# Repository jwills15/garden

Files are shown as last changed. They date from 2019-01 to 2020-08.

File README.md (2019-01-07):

# Smart Garden
Python code and engineering documentation for the Smart Garden system designed for Biola's Organic Garden.

All Python code can be located in the "Python Code/GardenPi" folder. The main script is tiltled "main.py".

Created by Joshua Williams, Engineering Research Intern, Biola CPE Department, Summer 2018.

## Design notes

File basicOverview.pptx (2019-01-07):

## Organic Garden Automation

Joshua Williams

## Current Solution

- Filling all gravel beds 15 minutes on, 45 minutes off
- Manual tank filling
- No oxygen level measurements

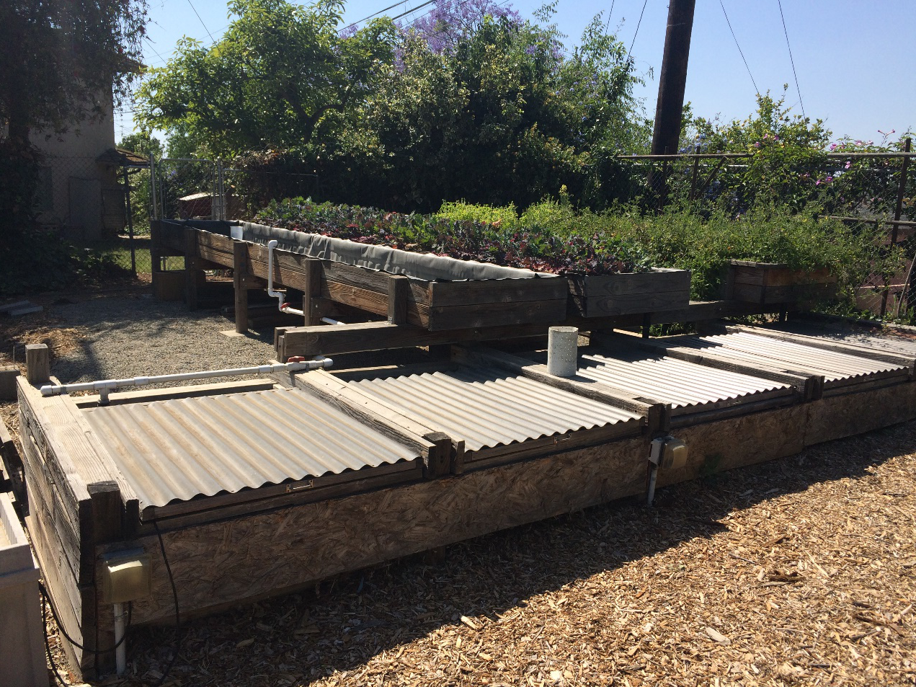
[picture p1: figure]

## Raspberry Pi

- Cheap computer
- 26 input and output ports
- WiFi enabled (Tweets)
- Programmable with Python

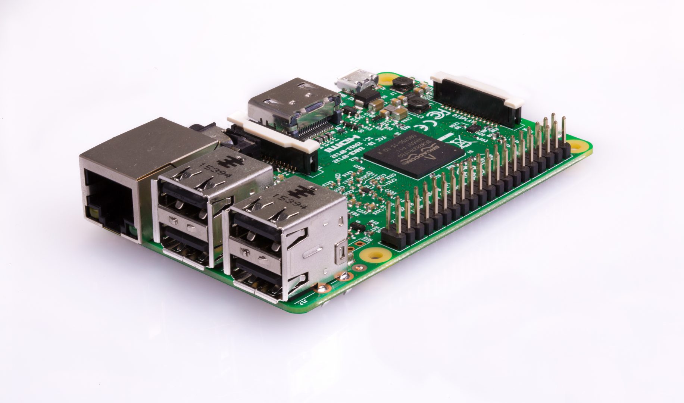
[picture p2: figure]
Image result for raspberry pi 3

## Gravel Beds

- Raspberry Pi software
- Turn on 1 valve every 15 minutes
- Other valves off 45 minutes
- 7am – 7pm

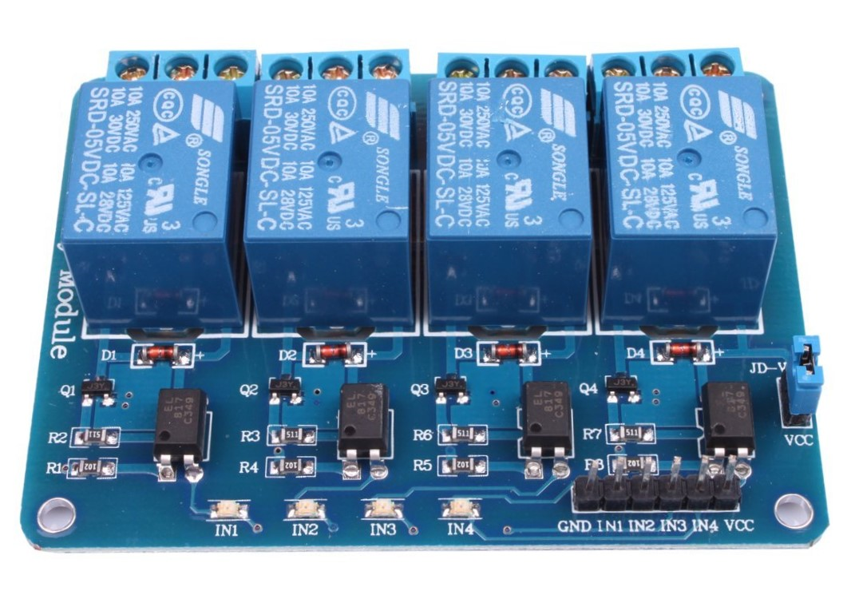
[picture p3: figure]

Raspberry Pi

Relay

Valve

## Dissolved Oxygen Sensor

- Measures oxygen level
- Turns on valve when low
- Sprinkler system to break water surface

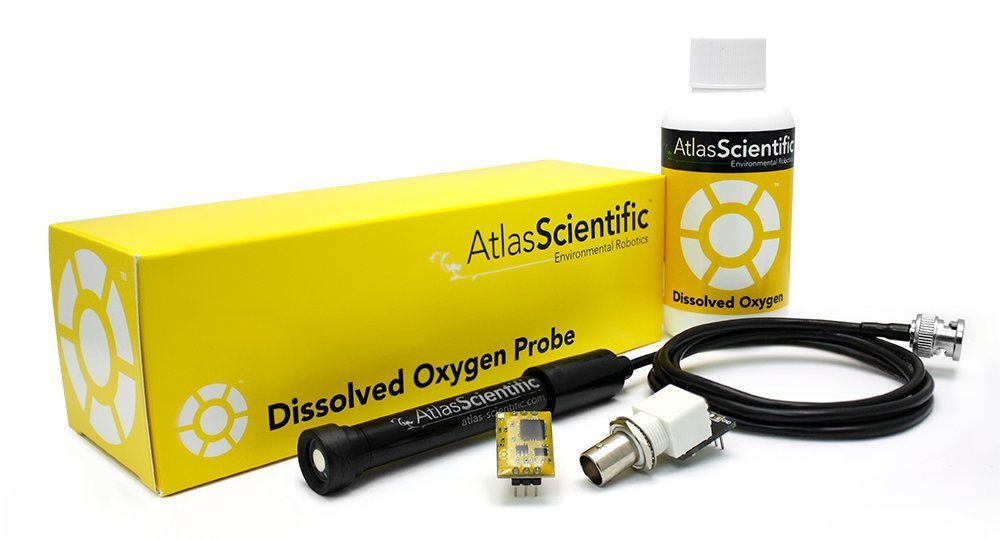
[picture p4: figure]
Image result for atlas dissolved oxygen sensor
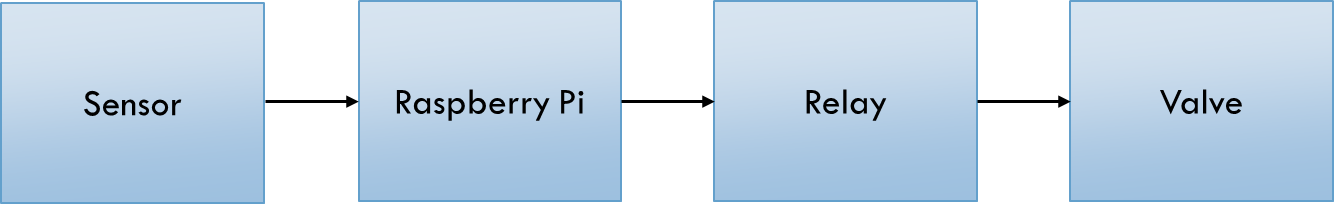
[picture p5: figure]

## Water Level Sensor

- Measures water level
- Turns on valve when low
- Turns off valve when at correct level

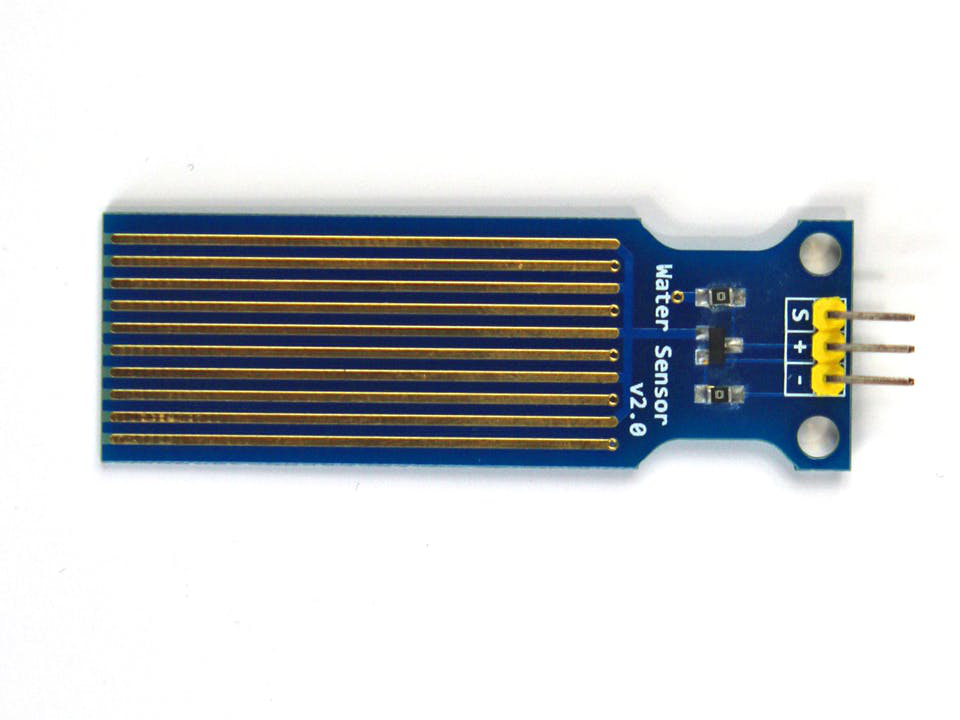
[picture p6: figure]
Image result for phantom water sensor

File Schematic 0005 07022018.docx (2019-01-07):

Project Number: 0005 | Project Name: Organic Garden Automation

## Document Revision

Date | Revision | Primary Author(s) | Notes
6/4/18 | 00 | Joshua Williams
7/2/18 | 01 | Joshua Williams | Added other sensors and components

5V 8-Channel Relay

Raspberry Pi GPIO Output

Python Script (Raspberry Pi, Raspbian)

Raspberry Pi GPIO Input

Gravel Bed Valves

Temperature Sensor

24VAC 50W Power Adapter

Sprinkler Valve

Tank Fill Valve

Dissolved Oxygen Sensor

Water Sensor

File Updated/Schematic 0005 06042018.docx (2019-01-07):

Project Number: 0005 | Project Name: Organic Garden Automation

## Document Revision

Date | Revision | Primary Author(s) | Notes
6/4/18 | 00 | Joshua Williams

24VAC 50W Power Adapter

Sprinkler Valve

5V 8-Channel Relay

Raspberry Pi GPIO Ports

Python Script (Raspberry Pi, Raspbian)

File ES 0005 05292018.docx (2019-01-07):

Project Number: 0005 | Project Name: Organic Garden Automation

## Document Revision

Date | Revision | Primary Author(s) | Notes
05/23/18 | 00 | Joshua Williams
5/29/18 | 01 | Joshua Williams | Made user needs and engineering specifications more specific

User Need | Engineering Specification | Notes
Must turn on one valve sequentially every 15 minutes which pumps water to the gravel beds, other valves are off | Software developed that turns on one valve every 15 minutes, turn off the valves for remaining 45 minutes of the hour, only one valve on at a time | Could write code so that every 15 minutes the sequential valve is turned on using if statements and counters
Pump water to gravel beds during only the day | Run pump from 7 am – 7 pm
Measure dissolved oxygen levels | Sensor measuring dissolved oxygen levels that is connectable to a controller and records values
Turn on sprinkler system when dissolved oxygen is too low in water | Software program that takes value from sensor, when level is below 4 mg/L turn on sprinklers, when level is above 7 mg/L turn off sprinklers | Could write code so that dissolved oxygen level is checked every time valves are modified
Notify when oxygen sprinklers are turned on/off | Software that sends some sort of message whenever sprinklers are modified
Measure water level in tank and turn on a valve or pump that fills the tank when it is too low, send a tweet to notify | Sensor that measures the water level | Could place sensor at water level, whenever does not sense water turn on pump
Fill the tank when water level is too low | Turn on some sort of pump that allows water to flow into tank when water level is measured as too low, turn off pump when water high enough | Could write code so that water level is checked every time valves are modified
Notify when water level pump is turned on/off | Software that sends some sort of message whenever water level pump is modified | Software not necessary for pump but necessary for notification

Engineering Specification

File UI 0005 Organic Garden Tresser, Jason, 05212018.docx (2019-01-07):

Interviewer Joshua Williams | Date 5/21/18
Project Title Organic Garden Automation | Project Number 0005

## Project Description

Organic garden has a 2000 gallon fish pond that contains tilapia and goldfish. The fish are fed externally and water is pumped into 4 raised gravel beds to provide oxygen and bacteria. The system must be monitored and operated electronically.

## User Background

### Name

Dr. Tresser

### Role

Organic Garden Manager

## Existing Solutions

Fish are fed externally, water is pumped from ponds to 4 raised gravel beds at the top of every hour during the day for 15 minutes, water is added manually when level gets low, water temperature is checked sporadically

## Use Case 1

- Pump is run constantly
- Valve is opened for one gravel bed at top of hour and runs for 15 min, then next valve for 15 min, etc, repeated every hour, not running at night
- System must open and close valves
- Valves provided are Orbit automatic in-line valves

## Use Case 2

- Sensor that monitors dissolved oxygen 24/7
- Low level of oxygen triggers a spray that causes surface of water to be broken, adding more oxygen to water
- Sprays must be turned off when oxygen level is sufficient
- Tweet notifying that the sprays were turned on or off

## Use Case 3

- Sensor measuring water level 24/7
- Turning on pump to fill the tank when water is too low
- Turning off pump when water level is sufficient
- Tweet notifying that the pump was turned on or off

## Problem Observed

Current systems are manual, they must be replaced by automatic sensors that perform the same functions

## Takeaways

Solution is completely software related with an installation of a few sensors

## Opportunities

Introducing a raspberry pi with sensors would be able to control the systems necessary with appropriate software

## Also Seen

Must have knowledge of a raspberry pi and how to integrate sensors

User Interview

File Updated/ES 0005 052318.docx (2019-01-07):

Project Number: 0005 | Project Name: Organic Garden Automation

## Document Revision

Date | Revision | Primary Author(s) | Notes
05/23/18 | 00 | Joshua Williams

User Need | Engineering Specification | Notes
Must turn on one valve sequentially every 15 minutes, other valves are shut off, only running during the day | Software program for raspberry pi must be developed that turns on one valve every 15 minutes, turn off the valves for remaining 45 minutes of the hour, only one valve on at a time, running from 7 am – 7 pm | Could write code so that every 15 minutes the sequential valve is turned on using if statements and counters
Measure dissolved oxygen levels and turn on a valve for a sprinkler system when it is too low, send a tweet to notify | Sensor measuring dissolved oxygen levels, when level is below 4 mg/L have the sprinklers turn on, when level is above 7 mg/L have the sprinklers turn off, send a tweet whenever sprinklers are turned on or off, controlled by raspberry pi and connected to GPIO | Could write code so that dissolved oxygen level is checked every time valves are modified
Measure water level in tank and turn on a valve or pump that fills the tank when it is too low, send a tweet to notify | Sensor that measures the water level, place sensor at appropriate level, when water level is above sensor have pump off, when water level is below sensor turn pump on, send a tweet whenever the pump is turned on or off | Could write code so that water level is checked every time valves are modified, raspberry pi not necessary for pump but necessary for tweet

Engineering Specification

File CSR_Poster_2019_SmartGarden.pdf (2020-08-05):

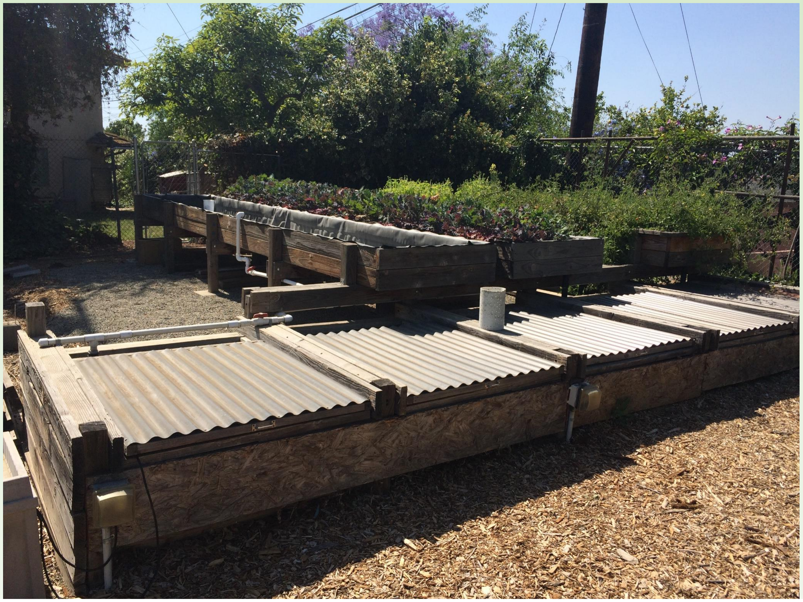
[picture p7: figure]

RESEARCH POSTER PRESENTATION DESIGN © 2015
www.PosterPresentations.com

# B.S. Engineering Physics, CPE Department

# Joshua Williams

# Biola’s Smart Garden

Biola’s Organic Garden contains a fish pond and plants that have very specific monitoring and watering needs. No existing solution is able to meet the requirements of watering specific plants at specified intervals while interfacing with sensors to regulate the fish pond. Previously, all watering and monitoring were performed manually. A programmed Raspberry Pi is the perfect solution to monitor and maintain the Organic Garden. Raspberry Pi’s are cost-efficient, support inputs and outputs, and are easily programmed. In this research, the Raspberry Pi was programmed to control valves in the garden’s sprinkler system, allowing individual plant beds to be watered at specific intervals. The system also monitors the fish pond by interfacing with a temperature sensor, a water level sensor, and a dissolved oxygen level sensor. System sensor values were tested against separate instruments to ensure accuracy. The system is headless, meaning it can be connected to over the internet by any device with the appropriate software and login, allowing remote system monitoring and maintenance. All activities performed by the system are logged and can be viewed online, while important alerts are notified over the Internet. A voice-controlled device is programmed to connect to the Raspberry Pi, allowing garden status updates to be accessed by asking, “how is my garden doing?”

## ABSTRACT

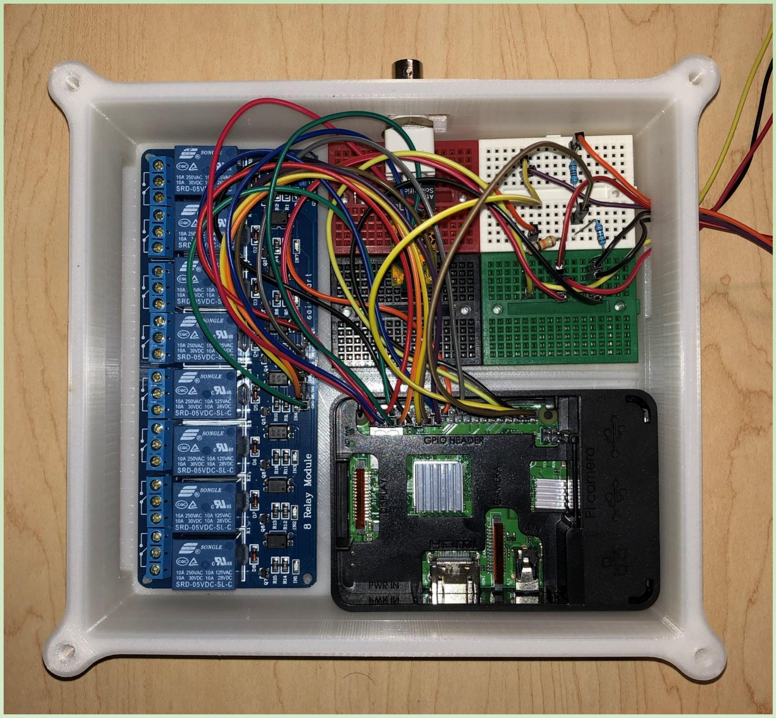
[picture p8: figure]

## OBJECTIVES

The Raspberry Pi was selected to accomplish the desired objectives. Raspberry Pis are very inexpensive microcontrollers which have substantial processing power coupled with a large number of general purpose input output (GPIO) ports. A new Raspberry Pi was bought and a fresh install of Raspbian was loaded onto its SD card. All programming was done in Python 3 using the default IDLE Python editor.
A. Watering of Gravel Beds
The valves connected to the watering system in the garden require AC power, so an AC power adapter powers the valves. To control the valves, a 5V relay board is connected to the Raspberry Pi. Each input on the relay board was assigned an appropriate GPIO pin, as shown in Figure 2. When the GPIO pin for the respective valve is activated, the relay closes and the valve opens. The main Python script was programmed to store the value of which valve is activated. When the script is run again, the code increments to the next valve. The default value for each GPIO output is high, which is changed to low to activate the relay and allow power to the valve.
B. Maintenance of Dissolved Oxygen Level
The Atlas Scientific Dissolved Oxygen Probe was selected to connect to the Raspberry Pi and measure the dissolved oxygen in the tilapia pond. The desired dissolved oxygen level is above 6.00 mg/L. The sensor was connected as shown in Figure 3 and the Python script was adjusted to measure the dissolved oxygen level every 15 minutes. When the level is measured to be too low, GPIO pin 16 is set to low, triggering the relay that is connected to valve 5. Valve 5 controls the water in a “sprinkler system” pipe directly above the surface of the tilapia pond. When water flows through the pipe, water sprinkles down and breaks the surface of the pond, adding dissolved oxygen to the water. When the dissolved oxygen reaches an appropriate level, the relay is opened and the valve is closed.

## GENERAL PROCEDURES

C. Maintenance of Pond Water Level
The water level of the pond frequently decreases due to evaporation and must be adjusted. Every 15 minutes, the water level is measured by an ultrasonic sensor. The distance from the sensor to the surface of the water is stored by the main Python script, allowing the water depth to be extrapolated. The schematic of the sensor is shown in Figure 4. If the water level is too low, pin 22 is changed to low, causing relay 6 to close and power valve 6. Valve 6 is connected to a water line which fills the tilapia pond. When the sensor measures that the water level has reached an appropriate level, the relay switches off and the valve closes.
D. Monitoring of Pond Water Temperature
The tilapia pond water must maintain a temperature above 65° F. To monitor the temperature, a waterproof thermometer sensor was connected to the Raspberry Pi, as shown in Figure 5. The main Python script was modified to record the temperature every 15 minutes. When the temperature falls below 65° F, an alert is sent out. Only one temperature alert can be sent per day.
E. Notification of Important System Events
The system administrator must be notified whenever the system discovers an issue and takes steps to correct it. To notify the administrator, the Python script was connected to a Twitter account. Tweets are sent out when the pond is being filled, when the water’s dissolved oxygen level is low, and when the temperature of the water is low.
F. System Access and Garden Status Updates
Since the system is located in a remote location, steps needed to be taken to ensure remote access to the system. The Raspberry Pi was configured to run headless. Connecting to the Raspberry Pi is identical to connecting the system to a monitor, with the connected device providing the inputs. Furthermore, an Amazon Echo Dot was configured to communicate with the Raspberry Pi. The status of the garden can be accessed by asking the Echo Dot, “Alexa, how is my garden doing?” The Echo Dot will then read back the most recent sensor values along with which relays are currently open. Amazon Echo Dot compatibility is still being tested and has not achieved full functionality.
G. System Case
The system and components need to be protected from the environment. A 3D printed case was produced to encase the Raspberry Pi, relays, and other electrical components. The case is placed in the barn in the Organic Garden and is connected to the tilapia pond through sprinkler wire run through conduit. A 3D printed case was also developed to protect the ultrasonic sensor, which is located directly above the pond. Both cases were printed using PLA.
GENERAL PROCEDURES (cont.) | RESULTS

## REFERENCES

All pictures and figures in this report were produced by me, Joshua Williams. This report details the methods used to accomplish the desired objectives of this research project. Although this report did not directly draw information from sources other than myself, all daily activities and resources used to accomplish this research project are detailed within the laboratory notebook that was maintained to provide proper engineering documentation of the system. All code for the project can be found at github.com/jwills15/garden

## ACKNOWLEDGEMENTS

Dr. Jason Tresser, Associate Professor of Biological Sciences and supervisor of Biola’s Organic Garden.

Dr. Albert Yee, Associate Professor of Engineering and CPE Summer Engineering Internship Coordinator.

Professor Stanley Ng, Professor of Circuits I and Circuits II.

Nathan Coddington (B.S. Chemistry) and Jimmy Su (B.S. Engineering Physics) for designing the 3D printed cases needed for the system.

Dr. Behzad Varamini and the Stewart Science Honors Program.

Biola’s Organic Garden contains a tilapia pond connected to four gravel beds which grow a range of fruits and vegetables. The gravel beds drain into the pond. The system developed needed to accomplish a variety of regulatory and monitoring tasks for both the gravel beds and the fish pond.

A. Watering of Gravel Beds
The four gravel beds within the garden must be watered for 15 minutes every hour from the hours of 7:00 AM until 7:00 PM. Previously, a 24-hour outlet timer was used to water all four beds simultaneously for the first 15 minutes of every hour. However, the fish pond maintains the most stable level of nutrients when each gravel bed is filled separately. The system was designed to begin filling a new bed every 15 minutes, filling all four beds individually over the course of each hour.
B. Maintenance of Pond Dissolved Oxygen Level
Tilapia require a specific level of dissolved oxygen in the water they live in to survive, typically above 6.0 mg/L. There was no previous method for monitoring dissolved oxygen. The system developed needed to monitor the dissolved oxygen and take steps to maintain an appropriate level.
C. Maintenance of Pond Water Level
The water level of the pond frequently drops due to evaporation. The water level was formerly maintained manually. The system developed required autonomous maintenance of the pond’s water level.
D. Monitoring of Pond Water Temperature
Tilapia require a specific water temperature to prosper, ideally above 65°
F. No method previously existed for monitoring water temperature. The system developed necessitated monitoring of temperature and notification when the temperature drops below 65° F.

IN 1

IN 2

IN 3

IN 4

GND

VCC

Raspberry Pi Pins | Relay Board
Pin 6 (GND)
Pin 7 (GPIO 4)

Pin 11 (GPIO 17)

Pin 13 (GPIO 27)

Pin 15 (GPIO 22)

Pin 4 (5 V)

AC Power Adapter

Gravel Bed Valves

AC
AC

Valve 1

Valve 2

Valve 3

Valve 4

Figure 2. Schematic of gravel bed watering circuit.

Raspberry Pi Pins
Pin 1 (3.3 V)
Pin 3 (SDA)
Pin 5 (SCL)
Pin 9 (GND)

EZO Circuit
VCC
TX
RX
GND

PGND
PRB

6666666666666666666666666666666 666zzz

BNC Connector

Dissolved Oxygen
Probe

Pin 16 (GPIO 25) IN 5

Valve 5

Relay Board

SHIELD
CENTER

Figure 3. Schematic of dissolved oxygen maintenance circuit.

## DISCUSSION

Each system feature was tested individually to verify functionality. After passing individual tests, each feature was added to the main Python script and further tests were performed to ensure whole-system functionality. All features were successfully implemented and tested, barring comprehensive Echo Dot interfacing. Regardless, the system is ready for deployment and is currently awaiting necessary infrastructure within the garden to be installed.

This research broke new ground into combining technology with gardening. Technological advances have made the Raspberry Pi as strong as a basic computer while staying in a price range that is easily affordable. The utilization of a Raspberry Pi microcontroller to maintain a healthy garden and tilapia pond demonstrates the wide range of applications for modern devices. Furthermore, the system developed in this research has even greater capability and can be built upon as the Organic Garden expands and grows. This research also demonstrated the interfacing of a Raspberry Pi with an Amazon Echo Dot. These two fairly recent devices are not designed to interface together, but this research showed that it can be accomplished. In the future, interfacing between a Raspberry Pi and an Amazon device will likely be expanded as users realize the potential of systems that utilize both devices.

Raspberry Pi Pins
Pin 2 (5 V)
Pin 36 (GPIO 16)
Pin 38 (GPIO 20)

Pin 34 (GND)

Ultrasonic Sensor
VCC
TRIG
ECHO

GND

Pin 22 (GPIO 25) | IN 6

Valve 6

Relay Board

2kΩ

1kΩ

Figure 4. Schematic of water level maintenance circuit.

Figure 1. Image of the Organic Garden’s tilapia pond and gravel beds.

Figure 6. Image of the completed system within its 3D printed case.

Raspberry Pi GPIO Pins
Pin 32 (GPIO 12)

Pin 2 (5 V)

Pin 34 (GND)

Temperature Sensor
Yellow

Red

Black

10kΩ

Figure 5. Schematic of temperature monitoring circuit.

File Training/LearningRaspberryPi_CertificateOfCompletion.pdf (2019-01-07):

# Certificate of Completion

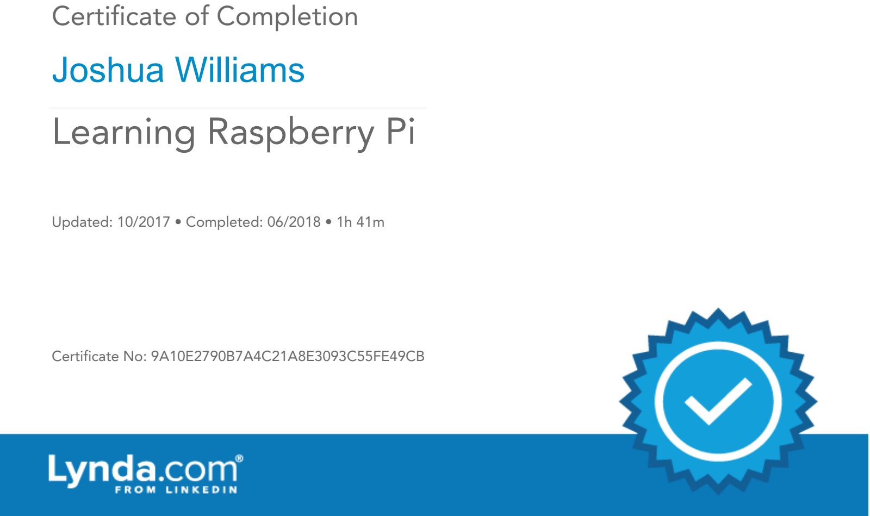
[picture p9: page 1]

# Joshua Williams

Updated: 10/2017 • Completed: 06/2018 • 1h 41m

Certificate No: 9A10E2790B7A4C21A8E3093C55FE49CB

# Learning Raspberry Pi

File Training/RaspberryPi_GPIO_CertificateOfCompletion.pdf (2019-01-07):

# Certificate of Completion

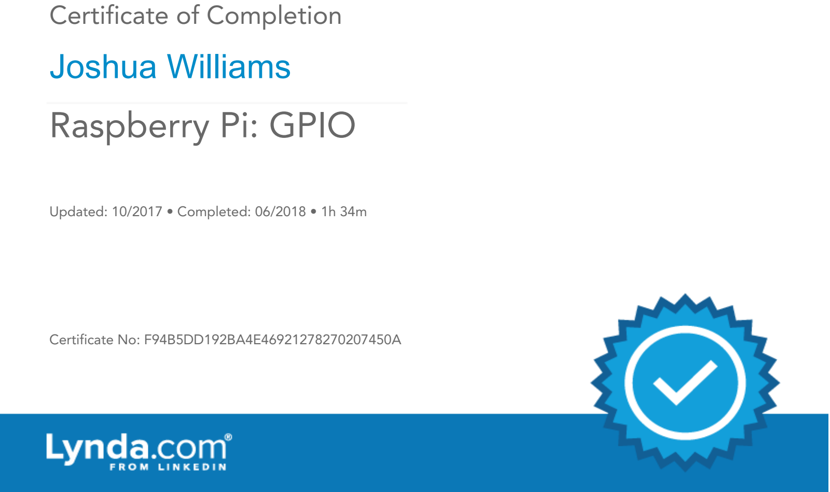
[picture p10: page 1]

# Joshua Williams

Updated: 10/2017 • Completed: 06/2018 • 1h 34m

Certificate No: F94B5DD192BA4E46921278270207450A

# Raspberry Pi: GPIO

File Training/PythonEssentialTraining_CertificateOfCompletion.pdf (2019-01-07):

# Certificate of Completion

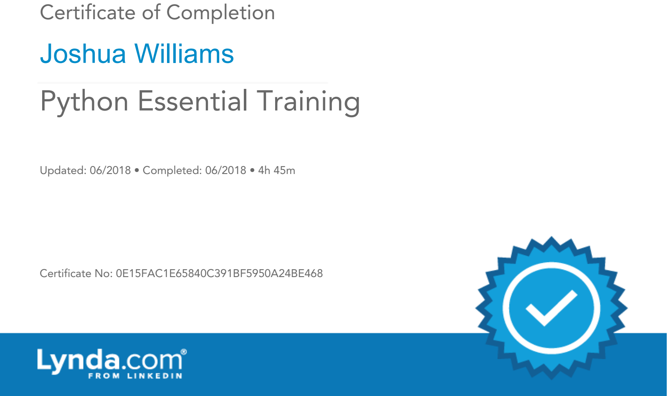
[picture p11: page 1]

# Joshua Williams

Updated: 06/2018 • Completed: 06/2018 • 4h 45m

Certificate No: 0E15FAC1E65840C391BF5950A24BE468

# Python Essential Training

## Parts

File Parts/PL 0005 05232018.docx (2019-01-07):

Project Number: 0005 | Project Name: Organic Garden Automation

Part Number | Description | Manufacturer | Quantity | Unit Price | Price
| Raspberry Pi 3 B+ Complete Kit, Amazon: https://goo.gl/ivNXbu | Canakit | 1 | $80 | $80
| | | | Total | $ 80.00

Parts List 05/23/2018

Parts List

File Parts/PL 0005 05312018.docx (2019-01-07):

Project Number: 0005 | Project Name: Organic Garden Automation

Part Number | Description | Manufacturer | Quantity | Unit Price | Price
MGT2450P | 24VAC 50W AC Power Adapter, Amazon: https://goo.gl/AtRcxk | MG Electronics | 1 | $19 | $19
101-70-102 | 5V 8-Channel Relay, Amazon: https://goo.gl/nRxFH7 | SainSmart | 2 | $11.50 | $23
| 50 ft 18/5 Sprinkler Wire, Home Depot: https://goo.gl/hv69d5 | Southwire | 1 | $24 | $24
| 20 Pack Waterproof Wire Connectors, Home Depot: https://goo.gl/QeP1Zn | DryConn | 1 | $8 | $8
| Raspberry Pi Jumper Wires, Amazon: https://goo.gl/9AehRi | Haitronic | 1 | $7 | $7
180903 | 35 ft 18 AWG White Wire, Amazon: https://goo.gl/1rZLP9 | Ancor | 1 | $6 | $6
| 32 GB Micro SDHC, Amazon: https://goo.gl/YnKSxc | Samsung | 1 | $15 | $15
| | | | Total | $ 102.00

Parts List 05/31/2018

Parts List

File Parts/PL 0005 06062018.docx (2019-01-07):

Project Number: 0005 | Project Name: Organic Garden Automation

Part Number | Description | Manufacturer | Quantity | Unit Price | Price
| Dissolved Oxygen Sensor, Amazon: https://goo.gl/My7ZDh | Atlas Scientific | 1 | $289.70 | 289.70
| 50 ft BNC Extension Cable, Amazon: https://goo.gl/LkVKYD | Phat Satellite | 1 | $18.99 | $18.99
| BNC Cable Connector, Amazon: https://goo.gl/eyiYSf | Valley | 1 | $4.95 | 4.95
RB-02S048 | Water Sensor, Amazon: https://goo.gl/a74Yyp | Phantom | 2 | $6.98 | $13.96
| | | | Total | $ 327.60

Parts List 6/6/18

Parts List

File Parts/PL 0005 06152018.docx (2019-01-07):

Project Number: 0005 | Project Name: Organic Garden Automation

Part Number | Description | Manufacturer | Quantity | Unit Price | Price
DS18B20 | Temperature Sensor for Raspberry Pi, Amazon: https://goo.gl/1StHkN | SUNKEE | 2 | $5.95 | $11.90
| Wire by the ft 18/10 Sprinkler Wire, Home Depot: https://goo.gl/GUZdvL | Southwire | 50 | $0.90 | $45.00
180903 | 35 ft 18 AWG Green Wire, Amazon: https://goo.gl/NefcKn | Ancor | 1 | $8.97 | $8.97
| | | | Total | $ 65.87

Parts List 06/15/2018

Parts List

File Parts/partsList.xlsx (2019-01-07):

Part | Manufacturer | Price | Quantity | Link
~~Raspberry Pi 3 B+~~ | ~~CanaKit~~ | ~~$80~~ | ~~1~~ | https://www.amazon.com/CanaKit-Raspberry-Starter-Premium-Black/dp/B07BCC8PK7
AC Power Adapter 24VAC | MG Electronics | $19 | 1 | https://www.amazon.com/MG-ELECTRONICS-MGT2450P-CLASS-TRANSFORMER/dp/B0010GR0A6?s=electronics
8 Channel Relay | SainSmart | $12 | 2 | https://www.amazon.com/SainSmart-101-70-102-8-Channel-Relay-Module/dp/B0057OC5WK?s=electronics
Sprinkler Wire | Southwire | $24 | Unknown | https://www.homedepot.com/p/Southwire-50-ft-18-5-Black-Solid-UL-Burial-Sprinkler-System-Wire-49275142/202316596
Jumper Wires | Haitronic | $7 | 1 | https://www.amazon.com/Haitronic-Multicolored-Breadboard-Arduino-raspberry/dp/B01LZF1ZSZ
Case
Wire Connectors | DryConn | $8 | 1 | https://www.homedepot.com/p/DryConn-Small-Waterproof-Wire-Connectors-Aqua-Orange-20-Pack-62114/202889871
18 AWG Wire | Ancor | $6 | 1 | https://www.amazon.com/Ancor-Marine-Grade-Primary-Battery/dp/B000NUYH5G
Backup SD Card | Samsung | $15 | 1 | https://www.amazon.com/Samsung-Class-Micro-Adapter-MB-MC32DA/dp/B00WR4IJBE
Dissolved Oxygen
Dissolved Oxygen Sensor | Atlas Scientific | $290 | 1 | https://www.amazon.com/Dissolved-Oxygen-Test-Kit-Hydroponics/dp/B005GRGPH4
BNC Cable Extender | Phat Satellite | $19 | 2 | https://www.amazon.com/SOLID-COPPER-JACKET-CORROSION-COMPRESSION/dp/B077PFCJ31?s=electronics
BNC Cable Adapter | Valley | $5 | 1 | https://www.amazon.com/niceEshop-Coupler-Adapters-Converter-Connector/dp/B002A6CWCQ?s=electronics
Water Level
Water Sensor | Phantom | $7 | 2 | https://www.amazon.com/Phantom-YoYo-Sensitivity-Water-Sensor/dp/B00A1AEJ9M?s=electronics
LEDs
Breadboard
Temperature?
Temp Sensor | Sunkee | $6 | 2 | https://www.amazon.com/SUNKEE-DS18B20-Temperature-Sensor-DS18B20DS18B20/dp/B008HODWBU
 |  |  |  | https://learn.adafruit.com/adafruits-raspberry-pi-lesson-11-ds18b20-temperature-sensing/hardware

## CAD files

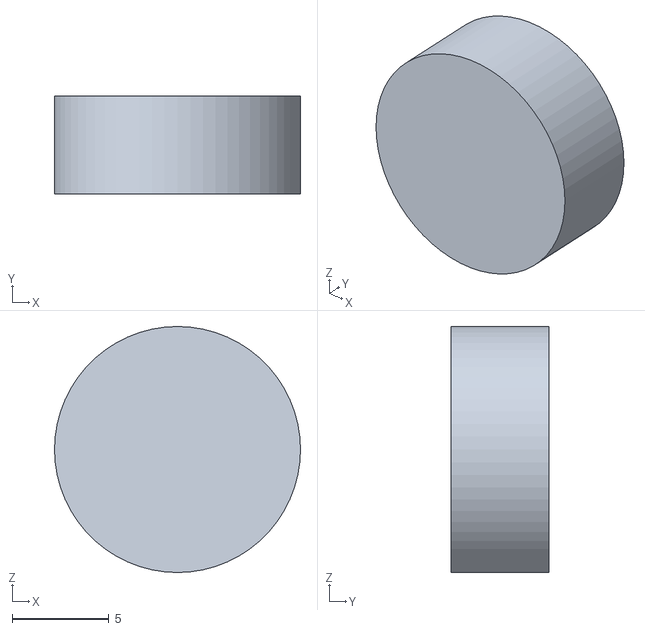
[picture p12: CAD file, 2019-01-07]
Case Print/Case Feet.STL
12.7 x 5.08 x 12.7

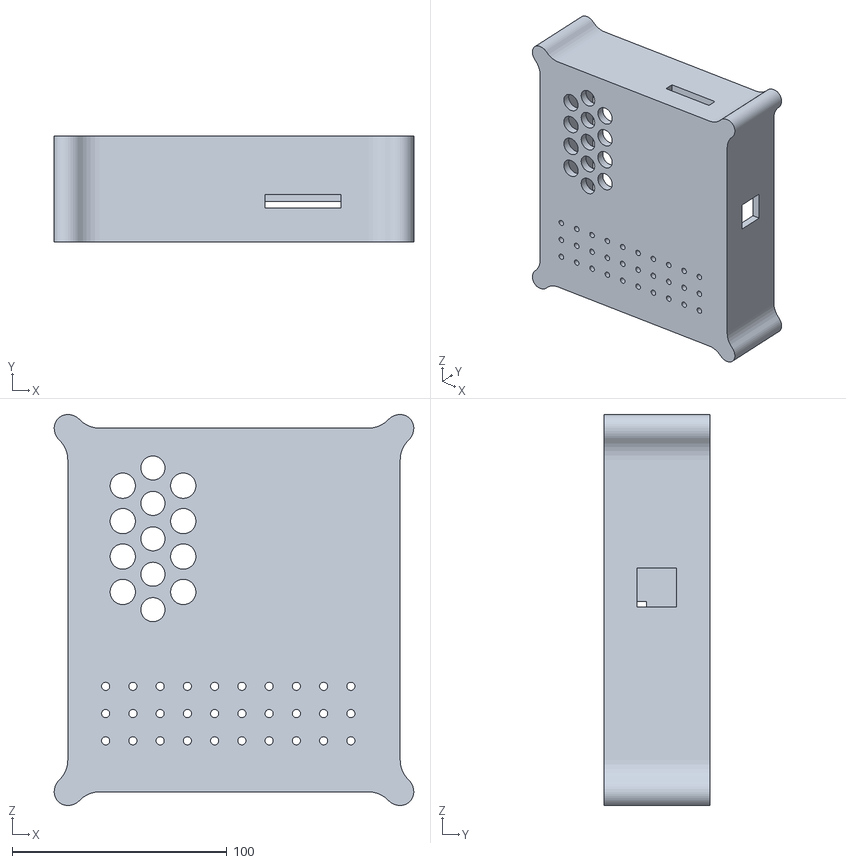
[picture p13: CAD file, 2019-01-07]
Case Print/GardenPi Case.STL
167.6 x 49.5 x 182.2

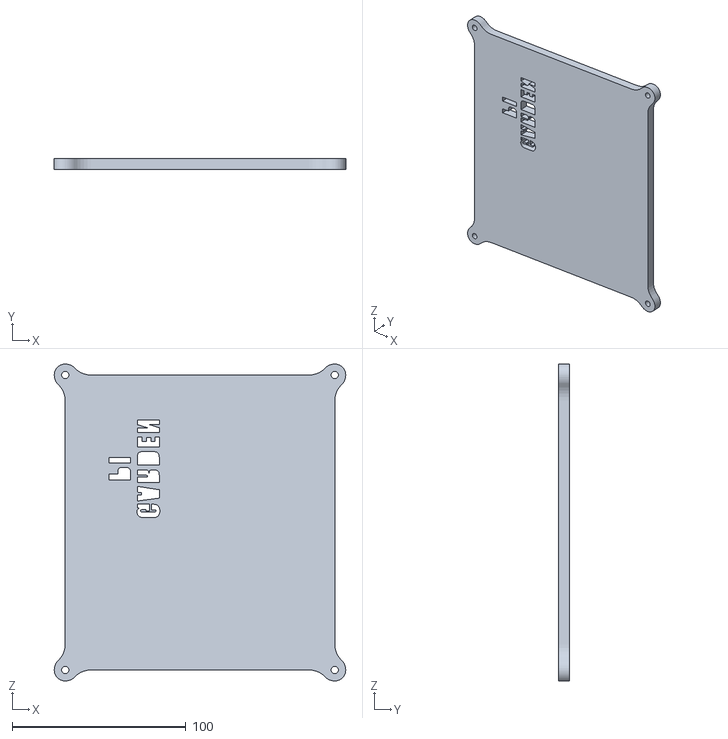
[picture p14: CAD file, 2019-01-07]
Case Print/Case Lid.STL
167.6 x 6.35 x 182.2

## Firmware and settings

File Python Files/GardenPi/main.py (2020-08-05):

#!/user/bin/python3

import os
import sys
import requests
import datetime
import time
import RPi.GPIO as GPIO
import configparser #module for the config file
import i2cPy3 #module that interfaces between i2c and DO sensor
from AWSIoTPythonSDK.MQTTLib import AWSIoTMQTTShadowClient # alexa 
from twython import Twython
GPIO.setwarnings(False)
GPIO.setmode(GPIO.BOARD)
import tkinter as tk
from tkinter import *
win=tk.Tk()
win.title('Garden Pi Status')
from w1thermsensor import W1ThermSensor 

## Output of High turns off valves, output of Low turns on valves

def load_config(filename='config.ini'):
    # opens the config file and tries to read it
    config = configparser.SafeConfigParser()
    this_dir = os.path.abspath(os.path.dirname(__file__))
    config.read(this_dir + '/' + filename)
    
    # checks to see if config file is in right place, if not gives error message
    if config.has_section('ValveConfig'):
        return {name:val for (name, val) in config.items('ValveConfig')}
    else:
        print('Unable to read file {} with section VavleConfig.'.format(filename))
        print('Make sure a file named config.ini lies in the directory {}.'.format(this_dir))
        raise Exception('Unable to find config file')


def load_bedConfig(filename='bed.ini'):
    # opens the file that keeps track of which bed is on
    bedConfig = configparser.SafeConfigParser()
    this_dir = os.path.abspath(os.path.dirname(__file__))
    bedConfig.read(this_dir + '/' + filename)

    # checks to see if bed config file is in right place, if not gives error message
    if bedConfig.has_section('CurrentBed'):
        return bedConfig
    else:
        print('Unable to read file {} with section CurrentBed.'.format(filename))
        print('Make sure a file named bed.ini lies in the directory {}.'.format(this_dir))
        raise Exception('Unable to find bed config file')


def tweet(message):
    # sends a tweet containing the message supplied
    C_key = "rRjHAXnZawtpqmbTwIqtws8SO"
    C_secret = "91Q7kDJefRor7Jg9Zp8HEX1oBTmPShDG4ORFndId4VhMNB8qOI"
    A_token = "1009920921820262400-GxLK5wZXE4AMR8ob5eSVNdWdjKfjyH"
    A_secret = "hKzwWsE240O2bKCcd0myGS90LiKnF4gDhPctowSijG6vx"

    try:
        myTweet = Twython(C_key, C_secret, A_token, A_secret)
        myTweet.update_status(status=message)
    except:
        # could not tweet due to error, logs error in bed valves log
        filePath = (os.path.abspath(os.path.dirname(__file__)) + '/Logs/' + date())
        if not os.path.exists(filePath):
            createLogs(filePath)
        with open(filePath + '/bedValvesLog', 'a') as log_file:
            log_file.write('\n{}: No internet connection. Could not tweet.\n\n'.format(currentTime()))


def alexa(config, doLevel, wlDistance, temp):
    try:
        # configure the values to be passed
        pinBed1 = int(config['gpio_bed1'])
        pinBed2 = int(config['gpio_bed2'])
        pinBed3 = int(config['gpio_bed3'])
        pinBed4 = int(config['gpio_bed4'])
        pinDO = int(config['gpio_do_sprinkler'])
        pinFill = int(config['gpio_fill'])
        GPIO.setup((pinBed1, pinBed2, pinBed3, pinBed4, pinDO, pinFill), GPIO.OUT)
        
        # gravel beds section
        bed = 1;
        if not GPIO.input(pinBed2):
            bed = 2
        elif not GPIO.input(pinBed3):
            bed = 3
        elif not GPIO.input(pinBed4):
            bed = 4

        # sprinklers section
        sprinklers = "off"
        if not GPIO.input(pinDO):
            sprinklers = "on"

        # water fill section
        fill = "off"
        if not GPIO.input(pinFill):
            fill = "on"

        # time updated
        updated = time.strftime("%A, %b %d %Y at %I:%M %p", time.localtime())

        # connects to alexa
        # Edit this to be the awshost you got from `aws iot describe-endpoint`
        awshost = "a3dgne3tku6c5g.iot.us-west-2.amazonaws.com"

        # Edit this to be your device name in the AWS IoT console
        thing = "gardenpi"

        awsport = 8883
        caPath = "aws-iot-rootCA.crt"
        certPath = "cert.pem"
        keyPath = "privKey.pem"
        # For certificate based connection
        myShadowClient = AWSIoTMQTTShadowClient(thing)
        myShadowClient.configureEndpoint(awshost, awsport)
        myShadowClient.configureCredentials(caPath, keyPath, certPath)
        myShadowClient.configureConnectDisconnectTimeout(60) 
        myShadowClient.configureMQTTOperationTimeout(10)  
        myShadowClient.connect()
        myDeviceShadow = myShadowClient.createShadowHandlerWithName("gardenpi", True)

        # sends to alexa
        tempreading = "{ \"state\" : { \"reported\": { \"updated\": \"%s\", \"bed\": \"%s\", \"temp\": \"%s\", \"oxygen\": \"%s\", \"sprinklers\": \"%s\", \"wlevel\": \"%s\", \"fill\": \"%s\" } } }" % (updated, str(bed), str('%.1f'%(temp)), str(doLevel), sprinklers, str('%.1f'%(wlDistance)), fill)
        myDeviceShadow.shadowUpdate(tempreading, None, 5)

    except:
        # could not talk to alexa due to error, logs error in bed valves log
        filePath = (os.path.abspath(os.path.dirname(__file__)) + '/Logs/' + date())
        if not os.path.exists(filePath):
            createLogs(filePath)
        with open(filePath + '/bedValvesLog', 'a') as log_file:
            log_file.write('\n{}: No internet connection. Could not update Alexa.\n\n'.format(currentTime()))
    
    
def nextValve(bedConfig, current):
    # defines the current valve and switches to the next sequential valve
    current += 1
    if current > 4:
        current = 1

    # changes file to record new current value and writes file
    bedConfig['CurrentBed']['current_valve'] = str(current)
    filePath = os.path.abspath(os.path.dirname(__file__)) + '/bed.ini'
    with open(filePath, 'w') as configfile:
        bedConfig.write(configfile)

    # returns the value of the new valve
    return currentValve(bedConfig)


def currentValve(bedConfig):
    # returns the current valve being used
    return int(bedConfig['CurrentBed']['current_valve'])


def runGravelBed(config, bedConfig, logFile, doLevel, wlDistance, temp):
    # sets the next valve and returns it
    current = nextValve(bedConfig, currentValve(bedConfig))
    pin = 0
    runtime = float(config['runtime_min'])

    # changes the pin to the GPIO pin for the current valve
    if current == 1:
        # run gravel bed 1
        pin = int(config['gpio_bed1'])
    elif current == 2:
         # run gravel bed 2
        pin = int(config['gpio_bed2'])
    elif current == 3:
        # run gravel bed 3
        pin = int(config['gpio_bed3'])
    elif current == 4:
        #run gravel bed 4
        pin = int(config['gpio_bed4'])

    # opens and writes to the log file
    with open(logFile, 'a') as log_file:
        try:
            # sets up the GPIO and changes from high to low and back
            GPIO.setup(pin, GPIO.OUT)
            log_file.write('{}: Turning on valve {}.\n'.format(currentTime(), current))
            GPIO.output(pin, GPIO.LOW)
            log_file.flush()
            # runs alexa and GUI update before call to sleep for duration of runtime
            alexa(config, doLevel, wlDistance, temp)
            UpdateGUI(config, doLevel, wlDistance, temp)
            # lets the valve run for the specified amount of time
            time.sleep(runtime * 60) #converts value to minutes
            log_file.write('{}: Turning off valve {}.\n'.format(currentTime(), current))
            GPIO.output(pin, GPIO.HIGH)
        # catches errors
        except Exception as ex:
            log_file.write('\n{}: An error occured on valve {}.\n{}\n\n'.format(currentTime(), current, ex))
            GPIO.output(pin, GPIO.HIGH)
            message = '{} {}: An error occured on valve {}. {}'.format(date(), currentTime(), current, ex)
            tweet(message)
        

def runDOsystem(config, logFile):
    # checks the level of dissolved oxygen and stores it
    doLevel = checkDO()
    # checks the minimum acceptable value of dissolved oxygen and the necessary GPIO pin
    doMin = float(config['do_min'])
    pin = int(config['gpio_do_sprinkler'])
    with open(logFile, 'a') as log_file:
        log_file.write('{}: Dissolved oxygen level- {} mg/L.\n'.format(currentTime(), doLevel))

        GPIO.setup(pin, GPIO.OUT)
        # keeps sprinkler on if level is too low
        if float(doLevel) < doMin and not GPIO.input(pin):
            log_file.write('{}: Dissolved oxygen is too low. Sprinklers are already on.\n'.format(currentTime()))
            GPIO.output(pin, GPIO.LOW)

        # turns on the sprinkler system if level is too low
        elif float(doLevel) < doMin:
            log_file.write('{}: Dissolved oxygen is too low. Turning on sprinklers.\n\n'.format(currentTime()))
            GPIO.output(pin, GPIO.LOW)
            message = '{} {}: Dissolved oxygen is too low. Turning on sprinklers.\n\n'.format(date(), currentTime())
            tweet(message)
            
        # checks to see if pin is already outputting high
        elif not GPIO.input(pin):
            log_file.write('{}: Dissolved oxygen has returned to normal. Turning off sprinklers.\n\n'.format(currentTime()))
            GPIO.output(pin, GPIO.HIGH)
            message = '{} {}: Dissolved oxygen has returned to normal. Turning off sprinklers.\n\n'.format(date(), currentTime())
            tweet(message)

        # do level is good and sprinklers are off
        else:
            GPIO.output(pin, GPIO.HIGH)

    return doLevel
            

def checkDO():
    # returns the value of the dissolved oxygen given by the sensor
    try:
        level = i2cPy3.main()
        return level
    except:
        logFile = (os.path.abspath(os.path.dirname(__file__)) + '/Logs/' + date() + '/DOsensorLog')
        with open(logFile, 'a') as log_file:
            log_file.write('{}: Dissolved oxygen sensor not found.\n'.format(currentTime()))
        message = '{} {}: Dissolved oxygen sensor not found.'.format(date(), currentTime())
        tweet(message)
        return -1


def runWaterLevel(config, logFile):
    waterLevelDistance = checkWL(config)
    pin = int(config['gpio_fill'])
    # TODO water level valve
    # grabs the desired distance of water height (in cm)
    waterLevelSetting = int(config['water_distance'])
    with open(logFile, 'a') as log_file:
        GPIO.setup(pin, GPIO.OUT)
        # turns on fill system if water level is too low
        if not GPIO.input(pin) and waterLevelDistance > waterLevelSetting:
            log_file.write('{}: Water level is too low. Fill is already on.\n'.format(currentTime()))
            GPIO.output(pin, GPIO.LOW)

        elif waterLevelDistance > waterLevelSetting:
            log_file.write('\n{}: Water level is too low. Turning on fill.\n'.format(currentTime()))
            GPIO.output(pin, GPIO.LOW)
            message = '{} {}: Water level is too low. Turning on fill.'.format(date(), currentTime())
            tweet(message)
            
        # checks to see if pin is already outputting high but water level is now good
        elif not GPIO.input(pin):
            log_file.write('{}: Water level has returned to normal. Turning off fill.\n\n'.format(currentTime()))
            GPIO.output(pin, GPIO.HIGH)
            message = '{} {}: Water level has returned to normal. Turning off fill.'.format(date(), currentTime())
            tweet(message)

        # water level is good and fill system is off
        else:
            GPIO.output(pin, GPIO.HIGH)
            log_file.write('{}: Water level is good.\n'.format(currentTime()))

    return waterLevelDistance


# checks the water level sensor
def checkWL(config):
    trig_pin = int(config['gpio_ultrasonic_trig'])
    echo_pin = int(config['gpio_ultrasonic_echo'])
    GPIO.setup(trig_pin, GPIO.OUT)
    GPIO.setup(echo_pin, GPIO.IN)

    # stores a timeout for if sensor is not found
    timeout = time.time() + 10; # 10 seconds
    sensorError = False;

    # sends out the trigger pulse
    GPIO.output(trig_pin, True)
    time.sleep(0.00001)
    GPIO.output(trig_pin, False)

    # stores the times to calculate the distance
    startTime = time.time();
    stopTime = time.time();
    # save the start time
    while GPIO.input(echo_pin) == 0:
        startTime = time.time()
        if time.time() > timeout:
            sensorError = True
            break
    # save time of arrival
    while GPIO.input(echo_pin) == 1:
        stopTime = time.time()
        if time.time() > timeout:
            sensorError = True
            break

    logFile = (os.path.abspath(os.path.dirname(__file__)) + '/Logs/' + date() + '/waterLevelLog')
    # checks if there was an error with the sensor
    if sensorError:
        with open(logFile, 'a') as log_file:
            log_file.write('{}: Ultrasonic sensor not found.\n'.format(currentTime()))
        message = '{} {}: Ultrasonic sensor not found.'.format(date(), currentTime())
        tweet(message)
        return -1
    # no problem with sensor, operate as normal
    else:
        # finds time difference
        timeElapsed = stopTime - startTime
        # find distance by multiplying with sonic speed 34300 cm/s (divide by 2 for there and back)
        distance = (timeElapsed * 34300) / 2

        with open(logFile, 'a') as log_file:
            log_file.write('{}: Water Distance- {} cm.\n'.format(currentTime(), '%.1f'%(distance)))

        return distance
    # TODO ultrasonic sensor


# checks the temperature of the water
def checkTemp():
    logFile = (os.path.abspath(os.path.dirname(__file__)) + '/Logs/' + date() + '/temperatureLog')
    try:
        sensor = W1ThermSensor()
        temperature_in_fahrenheit = sensor.get_temperature(W1ThermSensor.DEGREES_F)
        with open(logFile, 'a') as log_file:
            log_file.write('{}: Water Temperature- {} ºF.\n'.format(currentTime(), '%.1f'%(temperature_in_fahrenheit)))
        return temperature_in_fahrenheit
    except:
        with open(logFile, 'a') as log_file:
            log_file.write('{}: Temperature sensor not found.\n'.format(currentTime()))
        message = '{} {}: Temperature sensor not found.'.format(date(), currentTime())
        tweet(message)
        return -1


# returns the date
def date():
    return datetime.datetime.now().strftime('%Y-%m-%d')
# returns the time
def currentTime():
    return datetime.datetime.now().strftime('%H:%M:%S')


def createLogs(filePath):
    # creates the log files for each day
    os.makedirs(filePath)
    with open((filePath + '/DOsensorLog'), 'a') as log_file1:
        log_file1.write('''Dissolved Oxygen Log File for {}
---------------------------------------
'''.format(date()))
    with open((filePath + '/waterLevelLog'), 'a') as log_file2:
        log_file2.write('''Water Level Log File for {}
---------------------------------------
'''.format(date()))
    with open((filePath + '/bedValvesLog'), 'a') as log_file3:
        log_file3.write('''Gravel Bed Log File for {}
---------------------------------------
'''.format(date()))
    with open((filePath + '/temperatureLog'), 'a') as log_file3:
        log_file3.write('''Temperature Log File for {}
---------------------------------------
'''.format(date()))
    

# creates a GUI that shows the status of the valves and the values of the sensors
def UpdateGUI(config, doLevel, wlDistance, temp):
    pinBed1 = int(config['gpio_bed1'])
    pinBed2 = int(config['gpio_bed2'])
    pinBed3 = int(config['gpio_bed3'])
    pinBed4 = int(config['gpio_bed4'])
    pinDO = int(config['gpio_do_sprinkler'])
    pinFill = int(config['gpio_fill'])
    GPIO.setup((pinBed1, pinBed2, pinBed3, pinBed4, pinDO, pinFill), GPIO.OUT)
    
    # gravel beds section
    label_gravelBeds = tk.Label(win, text='Gravel Beds', relief = RAISED, width=30, font = ('Helvetica', 24)).grid(row=0,column=0, columnspan=2)
    label_bed1 = tk.Label(win, text='Bed 1', relief = RIDGE, width=15, font = ('Helvetica', 20)).grid(row=1,column=0)
    label_bed2 = tk.Label(win, text='Bed 2', relief = RIDGE, width=15, font = ('Helvetica', 20)).grid(row=2,column=0)
    label_bed3 = tk.Label(win, text='Bed 3', relief = RIDGE, width=15, font = ('Helvetica', 20)).grid(row=3,column=0)
    label_bed4 = tk.Label(win, text='Bed 4', relief = RIDGE, width=15, font = ('Helvetica', 20)).grid(row=4,column=0)
    if not GPIO.input(pinBed1):
        label_bed1_status = tk.Label(win, text='ON', relief = SUNKEN, width=15, bg='green', font = ('Helvetica', 20)).grid(row=1,column=1)
    else:
        label_bed1_status = tk.Label(win, text='OFF', relief = SUNKEN, width=15, bg='red', font = ('Helvetica', 20)).grid(row=1,column=1)
    
    if not GPIO.input(pinBed2):
        label_bed2_status = tk.Label(win, text='ON', relief = SUNKEN, width=15, bg='green', font = ('Helvetica', 20)).grid(row=2,column=1)
    else:
        label_bed2_status = tk.Label(win, text='OFF', relief = SUNKEN, width=15, bg='red', font = ('Helvetica', 20)).grid(row=2,column=1)

    if not GPIO.input(pinBed3):
        label_bed3_status = tk.Label(win, text='ON', relief = SUNKEN, width=15, bg='green', font = ('Helvetica', 20)).grid(row=3,column=1)
    else:
        label_bed3_status = tk.Label(win, text='OFF', relief = SUNKEN, width=15, bg='red', font = ('Helvetica', 20)).grid(row=3,column=1)

    if not GPIO.input(pinBed4):
        label_bed4_status = tk.Label(win, text='ON', relief = SUNKEN, width=15, bg='green', font = ('Helvetica', 20)).grid(row=4,column=1)
    else:
        label_bed4_status = tk.Label(win, text='OFF', relief = SUNKEN, width=15, bg='red', font = ('Helvetica', 20)).grid(row=4,column=1)

    # dissolved oxygen sensor section
    label_gravelBeds = tk.Label(win, text='Dissolved Oxygen', relief = RAISED, width=30, font = ('Helvetica', 24)).grid(row=5,column=0, columnspan=2)
    label_DOlevel = tk.Label(win, text='Level', relief = RIDGE, width=15, font = ('Helvetica', 20)).grid(row=6,column=0)
    label_DOvalve = tk.Label(win, text='Sprinklers', relief = RIDGE, width=15, font = ('Helvetica', 20)).grid(row=7,column=0)
    label_DOlevel_status = tk.Label(win, text='{} mg/L'.format(doLevel), relief = SUNKEN, bg='white', width=15, font = ('Helvetica', 20)).grid(row=6,column=1)
    if not GPIO.input(pinDO):
        label_DOvalve_status = tk.Label(win, text='ON', relief = SUNKEN, width=15, bg='green', font = ('Helvetica', 20)).grid(row=7,column=1)
    else:
        label_DOvalve_status = tk.Label(win, text='OFF', relief = SUNKEN, width=15, bg='red', font = ('Helvetica', 20)).grid(row=7,column=1)

    # water level section
    label_waterLevel = tk.Label(win, text='Water Level', relief = RAISED, width=30, font = ('Helvetica', 24)).grid(row=8,column=0, columnspan=2)
    # TODO water level distance section
    label_waterDistance = tk.Label(win, text='Distance', relief = RIDGE, width=15, font = ('Helvetica', 20)).grid(row=9,column=0)
    label_waterDistance_status = tk.Label(win, text='{} cm'.format('%.1f'%(wlDistance)), relief = SUNKEN, bg='white', width=15, font = ('Helvetica', 20)).grid(row=9,column=1)
    label_fillValve = tk.Label(win, text='Filling', relief = RIDGE, width=15, font = ('Helvetica', 20)).grid(row=10,column=0)
    if not GPIO.input(pinFill):
        label_fillValve_status = tk.Label(win, text='ON', relief = SUNKEN, width=15, bg='green', font = ('Helvetica', 20)).grid(row=10,column=1)
    else:
        label_fillValve_status = tk.Label(win, text='OFF', relief = SUNKEN, width=15, bg='red', font = ('Helvetica', 20)).grid(row=10,column=1)

    # temperature section
    label_temperature = tk.Label(win, text='Water Temperature', relief = RAISED, width=30, font = ('Helvetica', 24)).grid(row=11,column=0, columnspan=2)
    label_currentTemp = tk.Label(win, text='Current Temp', relief = RIDGE, width=15, font = ('Helvetica', 20)).grid(row=12,column=0)
    # TODO change color depending on temp
    if temp < int(config['temp_min']):
        label_currentTemp_status = tk.Label(win, text='{} ºF'.format('%.1f'%(temp)), relief = SUNKEN, width=15, bg='red', font = ('Helvetica', 20)).grid(row=12,column=1)
    else:
        label_currentTemp_status = tk.Label(win, text='{} ºF'.format('%.1f'%(temp)), relief = SUNKEN, width=15, bg='green', font = ('Helvetica', 20)).grid(row=12,column=1)

    label_buffer = tk.Label(win, text='DO NOT CLOSE GUI', relief = RAISED, width=30, bg='yellow', font = ('Helvetica', 24)).grid(row=13,column=0, columnspan=2)
    label_updated = tk.Label(win, text='Last Updated: {}'.format(currentTime()), relief = RAISED, width=30, bg='yellow', font = ('Helvetica', 24)).grid(row=14,column=0, columnspan=2)
    # updates the GUI before the sleep call
    win.update()
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

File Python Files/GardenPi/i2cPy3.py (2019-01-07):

#!/usr/bin/env python


##############################################################################
#
# Written by Dominic Bolding for the Raspberry Pi - 2017
#
# Website: myhydropi.com
# Contact: admin@myhydropi.com
#
# This code was written to help out a reader who wanted to send the sensor data
# using MQTT
# Feel free to use and modify this code for you own use in any way.
# atlas_i2c class code written by Atlas Scientific
#
##############################################################################


import io
import fcntl
from time import sleep




# Define Atlas Scientific Sensor Class




class atlas_i2c:


    long_timeout = 1.5  # the timeout needed to query readings & calibrations
    short_timeout = .5  # timeout for regular commands
    default_bus = 1  # the default bus for I2C on the newer Raspberry Pis,
                     # certain older boards use bus 0
    default_address = 97  # the default address for the Temperature sensor


    def __init__(self, address=default_address, bus=default_bus):
        # open two file streams, one for reading and one for writing
        # the specific I2C channel is selected with the bus
        # it is usually 1, except for older revisions where its 0
        # wb and rb indicate binary read and write
        self.file_read = io.open("/dev/i2c-" + str(bus), "rb", buffering=0)
        self.file_write = io.open("/dev/i2c-" + str(bus), "wb", buffering=0)


        # initializes I2C to either a user specified or default address
        self.set_i2c_address(address)


    def set_i2c_address(self, addr):
        # set the I2C communications to the slave specified by the address
        # The commands for I2C dev using the ioctl functions are specified in
        # the i2c-dev.h file from i2c-tools
        I2C_SLAVE = 0x703
        fcntl.ioctl(self.file_read, I2C_SLAVE, addr)
        fcntl.ioctl(self.file_write, I2C_SLAVE, addr)


    def write(self, string):
        # appends the null character and sends the string over I2C
        string += "\00"
        self.file_write.write(bytes(string, 'UTF-8'))


    def read(self, num_of_bytes=31):
        # reads a specified number of bytes from I2C,
        # then parses and displays the result
        res = self.file_read.read(num_of_bytes)  # read from the board
        # remove the null characters to get the response
        response = list([x for x in res])


        if(response[0] == 1):  # if the response isnt an error
            # change MSB to 0 for all received characters except the first
            # and get a list of characters
            char_list = [chr(x & ~0x80) for x in list(response[1:])]
            # NOTE: having to change the MSB to 0 is a glitch in the
            # raspberry pi, and you shouldn't have to do this!
            # convert the char list to a string and returns it
            result = ''.join(char_list)
            return result.split('\x00')[0]
        else:
            return "Error " + str(ord(response[0]))


    def query(self, string):
        # write a command to the board, wait the correct timeout,
        # and read the response
        self.write(string)


        # the read and calibration commands require a longer timeout
        if((string.upper().startswith("R")) or
           (string.upper().startswith("CAL"))):
            sleep(self.long_timeout)
        elif((string.upper().startswith("SLEEP"))):
            return "sleep mode"
        else:
            sleep(self.short_timeout)
        return self.read()


    def close(self):
        self.file_read.close()
        self.file_write.close()




def main():
        device = atlas_i2c(97)
        do_reading = device.query('R')
        return do_reading
        
        
if __name__ == '__main__':
    main()

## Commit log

2019-01-07 Initial
    Upload of all files as of 1/6/19.
    [Case Feet.STL, Case Lid.STL, GardenPi Case.STL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]
2020-08-05 Final Changes Jan 2020
    Replaced water sensor with ultrasonic sensor. Interfaced raspberry pi with Amazon Alexa.
    [main.py, ultrasonicSensor.py]
